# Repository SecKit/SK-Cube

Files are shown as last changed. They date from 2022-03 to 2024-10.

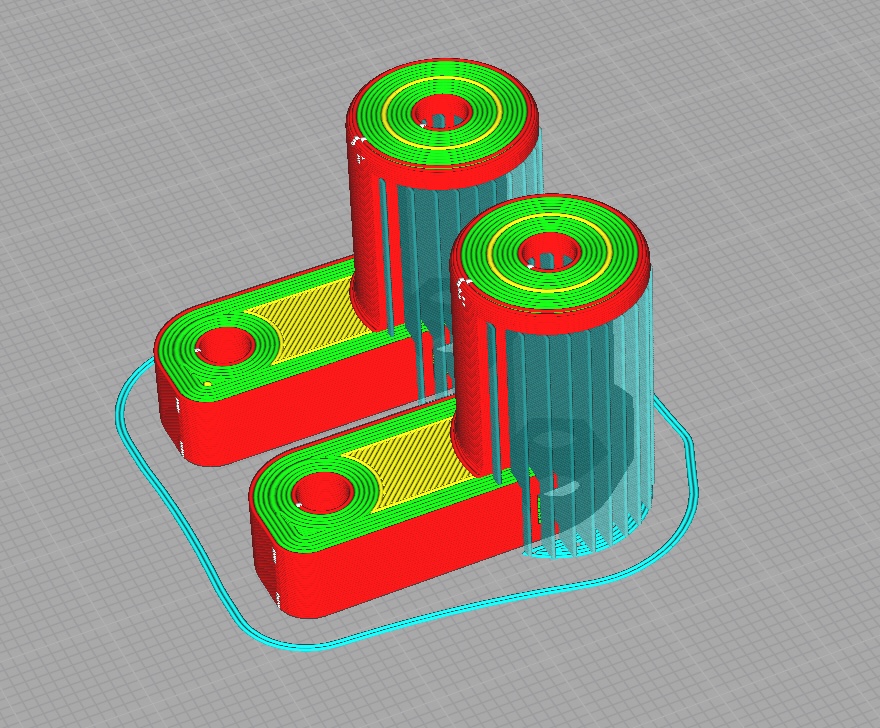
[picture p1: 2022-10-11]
STEP files/optional/secondary XY belt tensioner/z_slicing orientation.jpg

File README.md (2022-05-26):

## SK-Cube CoreXY 3D Printer

### Website
https://seckit3dp.design/price/sk-cube

### Wiki: Assembly Manual, tuning guide, etc.
https://sites.google.com/view/seckit-wiki/sk-cube-200x200x200/assembly-manual/sk-cube-assembly-manual

### Join SecKit's FaceBook group for owner's discussion and latest update
https://www.facebook.com/groups/SecKitCoreXY3DP/

### YouTube
https://www.youtube.com/channel/UCJUHiJfgDE5aeqbk4iZBPHA/videos

### FaceBook Page
https://www.facebook.com/seckit.3dp

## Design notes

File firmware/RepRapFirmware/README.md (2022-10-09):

1. Use a max 32G FAT32-format micro SD card. A 64GB or larger card is not supported.
2. Extract the zip file and copy all contents in "SK-Cube RRF" directory to the root of a micro SD card.
3. Follow the quick steps in the [Firmware Chapter](https://sites.google.com/view/seckit-wiki/sk-tank-350x350x400/assembly-manual/sk-tank-assembly-manual/12-firmware) of [SK-Tank Assembly Manual](https://sites.google.com/view/seckit-wiki/sk-tank-350x350x400/assembly-manual/sk-tank-assembly-manual) to flash the firmware to your control board.

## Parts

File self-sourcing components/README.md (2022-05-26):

Self-sourcing components for SK-Cube Barebones Kit.

|Category  |Item | #|Electrical req. |Mechanical req. |
|---|:---|-:|:---|:---|
|Power |Meanwell LRS-200-24 PSU | 1|200 or 350 watt, 24V output |4 holes on the bottom panel (PS.)|
|Power |SSR DC-AC | 1|At least 10 amp AC |2 holes on the bottom panel |
|Power |FS-101 fuse box and fuse | 1|6A for 110V. 3A for 220V. |1 hole on the bottom panel |
|Power |Power switch | 1| | |
|Power |Power cord | 1|At least 0.75 mm^2 internal wire |150cm or longer |
|Control |BigTreeTech Octopus or GTR | 1|At least 6 driver slots |4 holes on back panel |
|Control |TMC2225 | 6|(or other drivers) | |
|Stepper |NEMA17 1.8°/0.9° stepper for XY | 2|Common NEMA 17 stepper | |
|Stepper |NEMA17 1.8° pancake stepper for E | 1|Common NEMA 17 pancake stepper |(PPS.) |
|Extruder  |BMG or Hemera extruder | 1|(PPS.) | |
|Fan |4010 fan for driver cooling | 1|24V | |
|Fan |4020 blower for part cooling | 1|24V | |
|Sensor |Filament runout sensor | 1|(optional) | |
|Accessory |PTFE tube 3mm ID, 40cm | 1| | |
|Accessory |Cable tie |20| | |
|Accessory |Cable management nylon sleeve, wrapper, etc.| 1| | |

PS. Pre-drilled holes are there on the ACM (Aluminum Composite Material) back panel but you can still drill customized holes easily.

PPS. Use your preferred extruder and design a customized adapter based on [SK-Tank BMG adapter STEP file](https://github.com/SecKit/SK-Tank/tree/master/STEP%20files/extruder%20adapter%20-%20BMG) and [SK-Tank extruder carriage STEP file](https://github.com/SecKit/SK-Tank/tree/master/STEP%20files/extruder%20carriage). SK-Cube and SK-Tank share the same part cooling fan duct.

*SecKit will not be responsible for your self-sourcing items.*

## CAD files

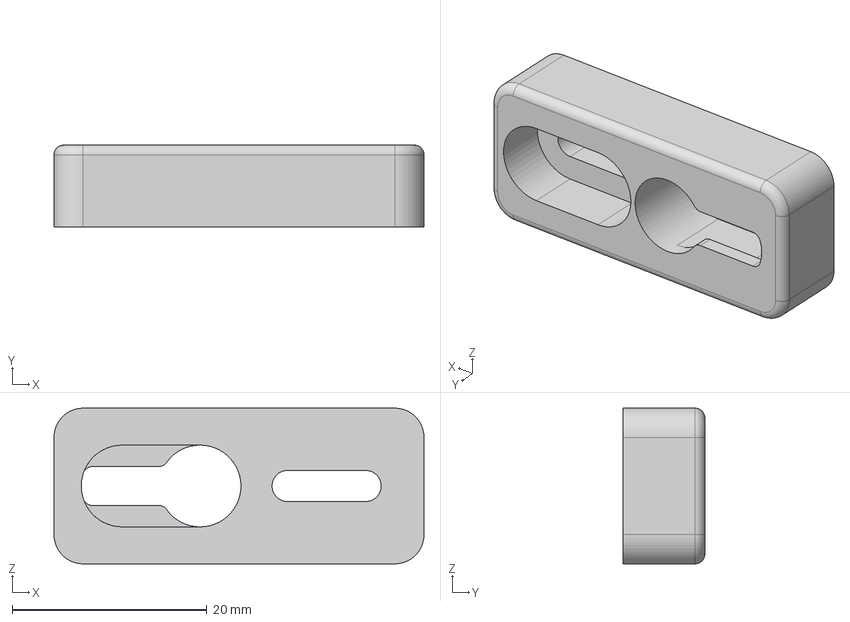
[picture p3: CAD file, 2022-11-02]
STEP files/must/bed expansion mount/bed expansion mount.step
38.0 x 8.40 x 16.0 mm

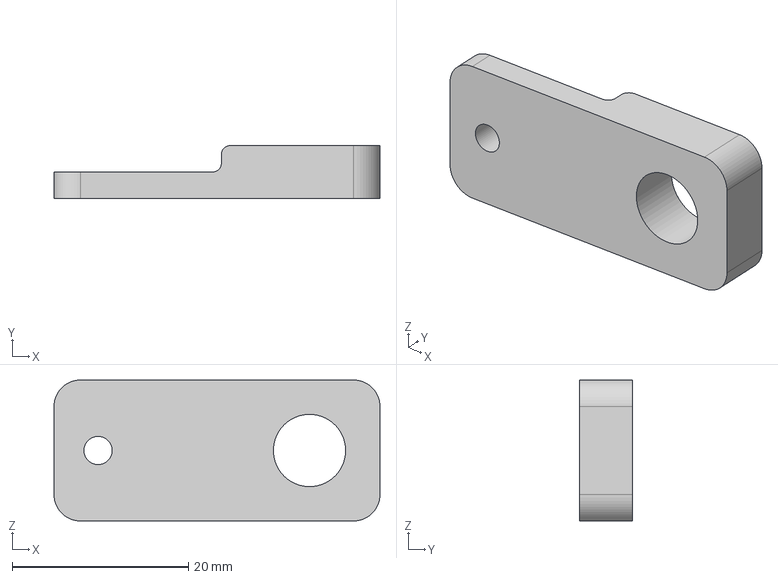
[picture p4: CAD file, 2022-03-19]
STEP files/must/bed fixed mount/bed fixed mount.step
37.0 x 6.00 x 16.0 mm

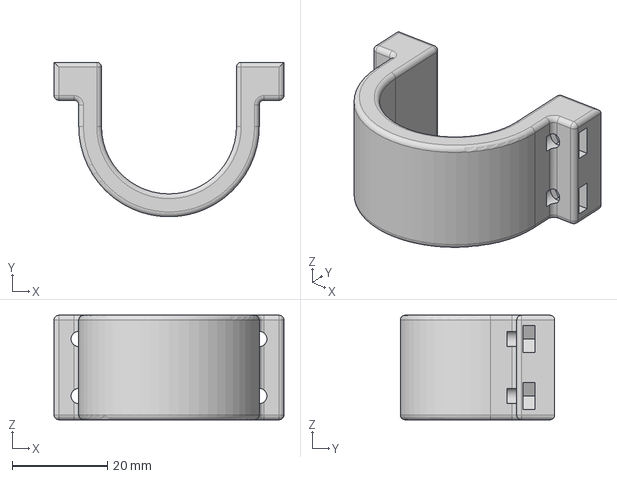
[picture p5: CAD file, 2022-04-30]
STEP files/must/Belted-Z stepper holder/NEMA8 gearbox bracket.step
48.4 x 32.5 x 22.0 mm

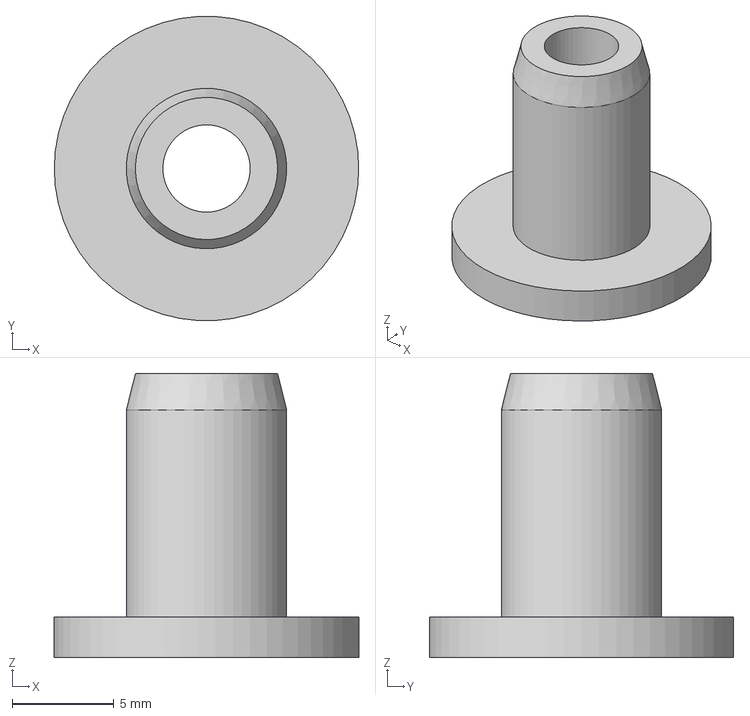
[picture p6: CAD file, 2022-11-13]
STEP files/must/filament PTFE guide holder/filament PTFE guide holder.step
15.0 x 15.0 x 14.0 mm

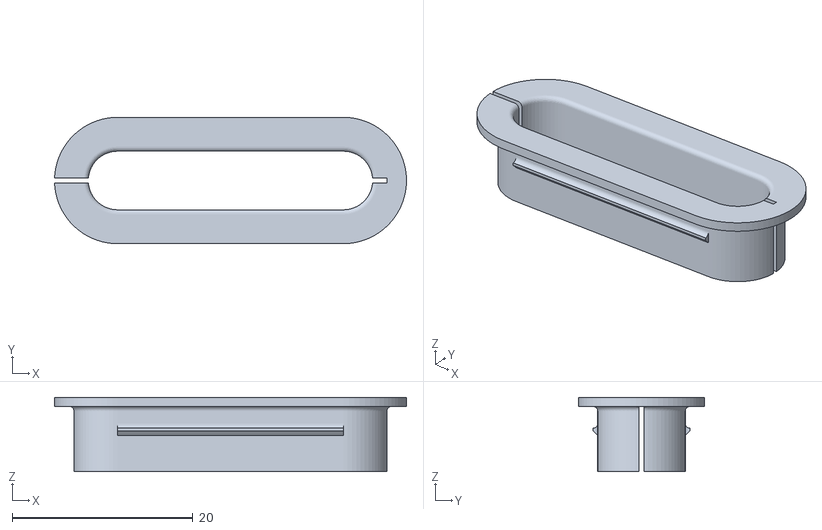
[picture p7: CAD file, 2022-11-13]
STEP files/must/grommets for wires/rear top.stl
39.0 x 14.0 x 8.20

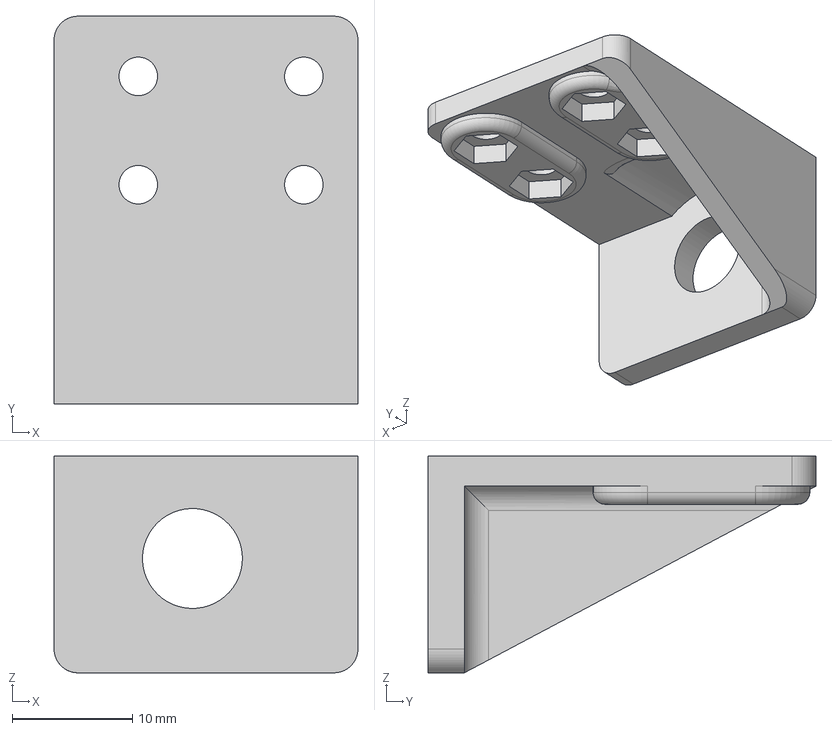
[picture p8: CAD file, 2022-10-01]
STEP files/must/inductive sensor mount/inductive sensor mount - Volcano hotend.step
25.3 x 32.2 x 18.0 mm

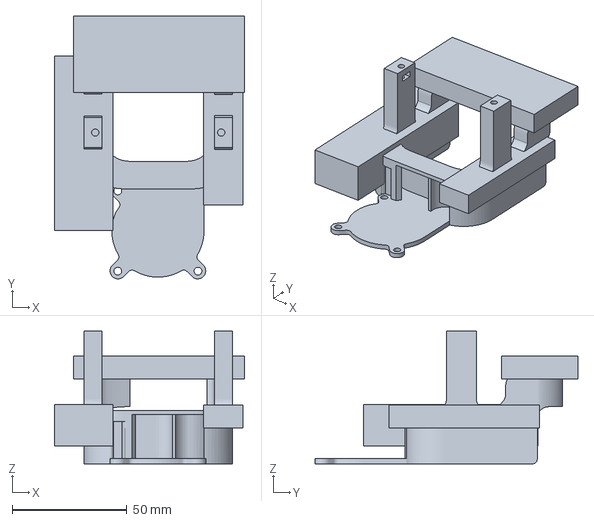
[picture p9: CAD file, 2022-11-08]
STEP files/must/part cooling fan duct/Volcano hotend/Cura 5.1.1 project of a SK-Cube fan duct + Volcano hotend.3mf
83.0 x 114.8 x 57.9 mm

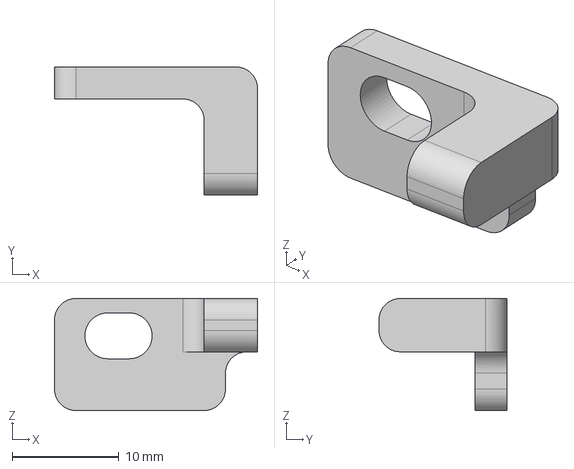
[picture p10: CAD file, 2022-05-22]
STEP files/must/X endstop finger/X endstop finger.step
19.0 x 12.0 x 10.5 mm

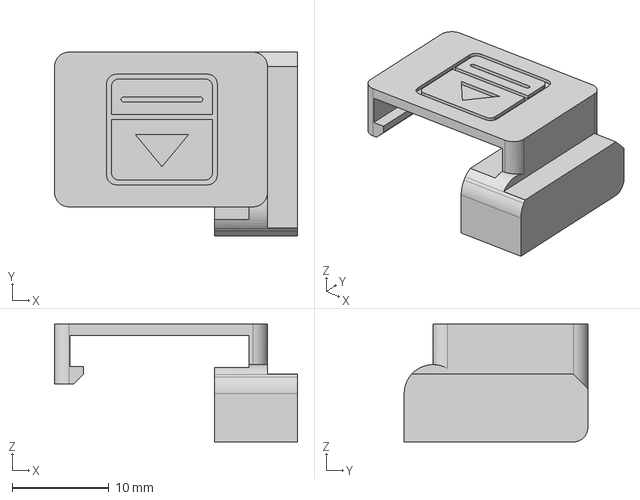
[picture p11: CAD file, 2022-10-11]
STEP files/must/X endstop trigger cap/X endstop trigger cap - for Breezer remote cooling duct.step
25.1 x 19.0 x 12.2 mm

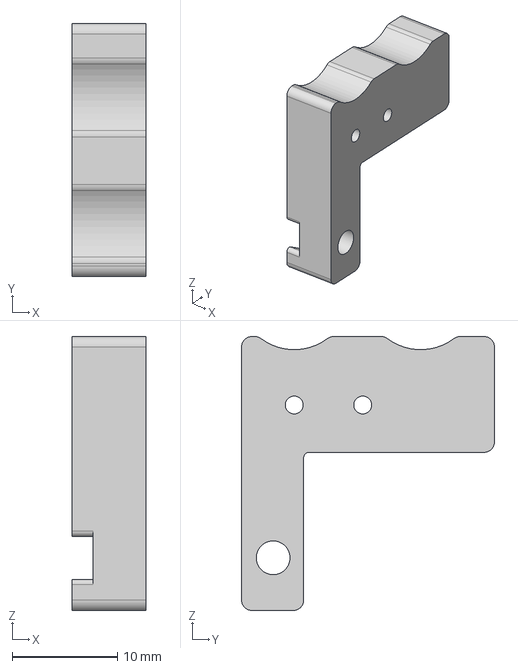
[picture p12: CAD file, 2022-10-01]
STEP files/must/Y-min endstop mount/Y-min endstop mount - right.step
7.00 x 24.0 x 26.0 mm

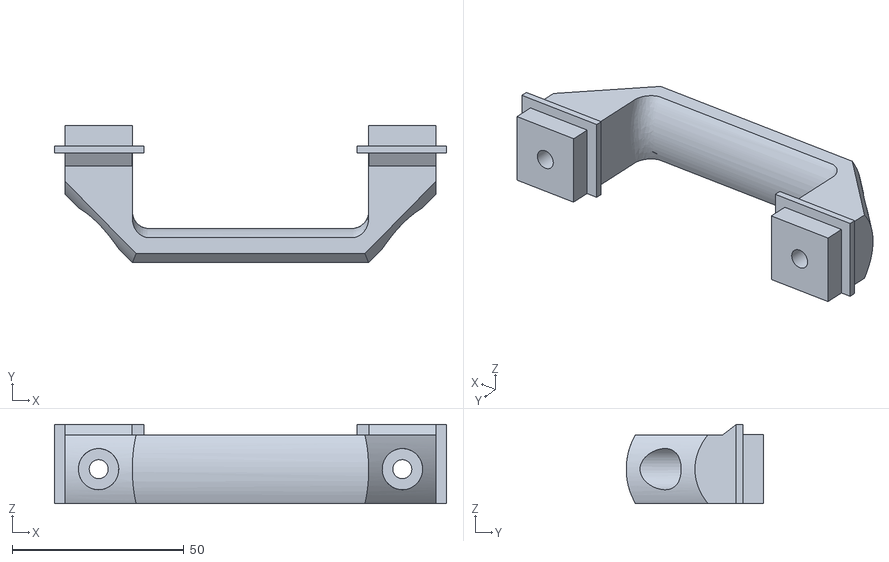
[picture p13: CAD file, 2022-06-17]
STEP files/optional/carry handle/handle_by Jeffery Kilgore.stl
114.0 x 40.0 x 23.0

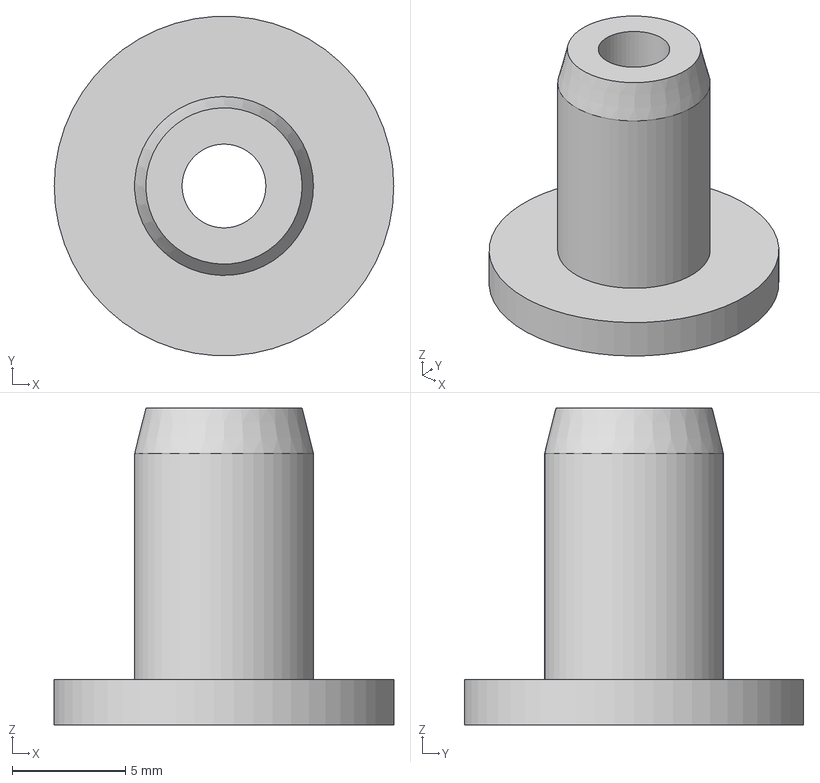
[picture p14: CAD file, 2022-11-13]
STEP files/optional/chamber thermistor holder/chamber temp sensor holder.step
15.0 x 15.0 x 14.0 mm

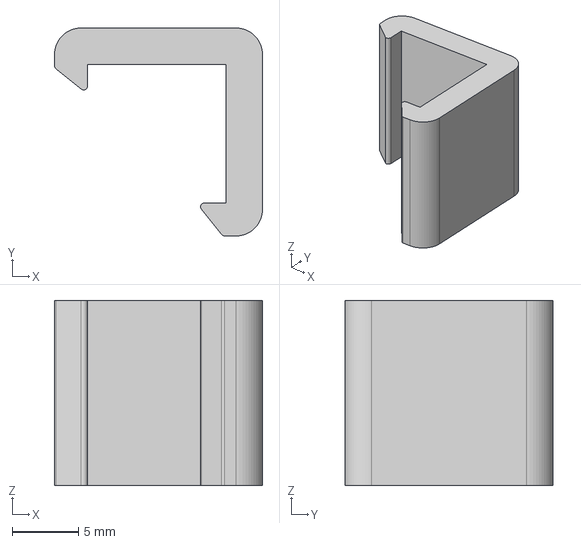
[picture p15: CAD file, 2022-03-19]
STEP files/optional/panel clamp/panel clamp.step
15.7 x 15.7 x 14.0 mm

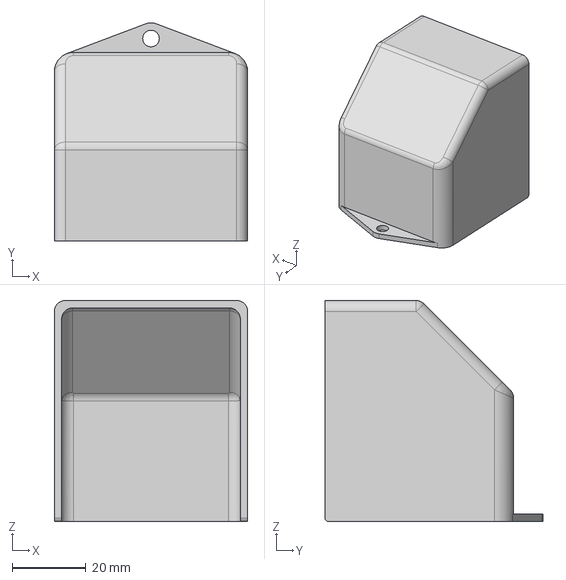
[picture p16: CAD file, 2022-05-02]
STEP files/optional/power switch cap/Power switch cap.step
52.5 x 59.2 x 60.0 mm

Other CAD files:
STEP files/optional/filament PTFE guide holder/filament PTFE guide holder.step
STEP files/optional/PTC heater box - easy print/panel_rear.stl
STEP files/optional/PTC heater box/Activated charcoal cartridge/3_0mm cover A.step
STEP files/optional/PTC heater box/PTC heater box.step
STEP files/must/Belted-Z stepper holder/NEMA8 gearbox bracket.stl
STEP files/must/Belted-Z stepper holder/square nut/NEMA8 gearbox bracket - square nut.step
STEP files/must/Belted-Z stepper holder/square nut/NEMA8 gearbox bracket - square nut.stl
STEP files/must/X endstop finger/X endstop finger.stl
STEP files/must/X endstop trigger cap/X endstop trigger cap - for Breezer remote cooling duct.stl
STEP files/must/X endstop trigger cap/X endstop trigger cap.step
STEP files/must/X endstop trigger cap/X endstop trigger cap.stl
STEP files/must/X endstop trigger cap/deprecated/X endstop finger.stl
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

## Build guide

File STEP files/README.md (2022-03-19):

Slicing tips

Printed files are all non-structural components so a common PLA or PETG filament with 0.4mm nozzle and 0.2mm layer height will do. Use ABS/ASA if your printer is enclosed. For special slicing settings please refer to the README.md file and print orientation pictures in each STL directory.   

All designs in this directory and subdirectories are shared under [CC BY-NC-SA 4.0](https://creativecommons.org/licenses/by-nc-sa/4.0/)

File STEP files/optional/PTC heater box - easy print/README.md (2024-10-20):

Slicer settings

|Setting |Description |
|:---|:---|
|Quantity |1 |
|Wall thickness |2mm |
|Infill |20% |
|Support |No |

ABS/ASA, 0.4mm nozzle, 0.2mm layer height

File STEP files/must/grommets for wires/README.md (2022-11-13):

Slicer settings

The gap in each grommet allows wire to pass after printer assembled.

|Setting |Description |
|:---|:---|
|Quantity |2, except the rear top one |
|Wall thickness |2mm |
|Infill |100% |
|Support |None |

PLA/PETG, 0.4mm nozzle, 0.2mm layer height

Use ABS/ASA if printer is enclosed.

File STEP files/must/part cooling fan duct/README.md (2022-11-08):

Slicer settings

|Setting |Description |
|:---|:---|
|Quantity |1 |
|Wall thickness |1.6 mm |
|Infill |40% |
|Support |20% with support blockers |

PLA/PETG, 0.4mm nozzle, 0.2mm layer height

Use ABS/ASA if printer is enclosed.

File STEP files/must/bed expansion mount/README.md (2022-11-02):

Slicer settings

|Setting |Description |
|:---|:---|
|Quantity |1 |
|Wall thickness |2mm |
|Infill |100% |
|Support |Yes |

PLA/PETG, 0.4mm nozzle, 0.2mm layer height

Use ABS/ASA if printer is enclosed.

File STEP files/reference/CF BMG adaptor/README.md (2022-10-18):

BMG adaptor is the plate between NEMA17 pancake stepper and BMG extruder, providing a mounting base to the CoreXY motion.

In case that some extruders have heat sink integrated so the overall length are shorter, you might have to lower the mounting holes for the stepper so the nozzle can still touch the build surface at Z=0.

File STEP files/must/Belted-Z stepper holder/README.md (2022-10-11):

Slicer settings

For kit sent after Oct 15, 2022, please use the square nut version. M3 square nuts are included in the kits.

|Setting |Description |
|:---|:---|
|Quantity |3 |
|Wall thickness |2.8mm |
|Infill |100% |
|Support |None |

PLA/PETG, 0.4mm nozzle, 0.2mm layer height

Use ABS/ASA if printer is enclosed.

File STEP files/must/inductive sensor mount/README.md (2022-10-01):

Slicer settings

Please choose the Volcano or the V6 version based on your hotend.

|Setting |Description |
|:---|:---|
|Quantity |1 |
|Wall thickness |2mm |
|Infill |100% |
|Support |None |

PLA/PETG, 0.4mm nozzle, 0.2mm layer height

Use ABS/ASA if printer is enclosed.

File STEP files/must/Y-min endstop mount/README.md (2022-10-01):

Slicer settings

Only the right one is necessary. The left one is optionally acting as a physical Y-min stopper.

|Setting |Description |
|:---|:---|
|Quantity |1 |
|Wall thickness |2mm |
|Infill |100% |
|Support |None |

PLA/PETG, 0.4mm nozzle, 0.2mm layer height

Use ABS/ASA if printer is enclosed.

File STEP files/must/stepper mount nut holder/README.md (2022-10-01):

Slicer settings

|Setting |Description |
|:---|:---|
|Quantity |2 |
|Wall thickness |2mm |
|Infill |20% |
|Support |None |

PLA/PETG, 0.4mm nozzle, 0.2mm layer height

Use ABS/ASA if printer is enclosed.

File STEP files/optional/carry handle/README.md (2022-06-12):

Slicer settings

|Setting |Description |
|:---|:---|
|Quantity |2 |
|Wall thickness |2mm |
|Infill |100% |
|Support |Optional |

PLA/PETG, 0.4mm nozzle, 0.2mm layer height

Use ABS/ASA if printer is enclosed.

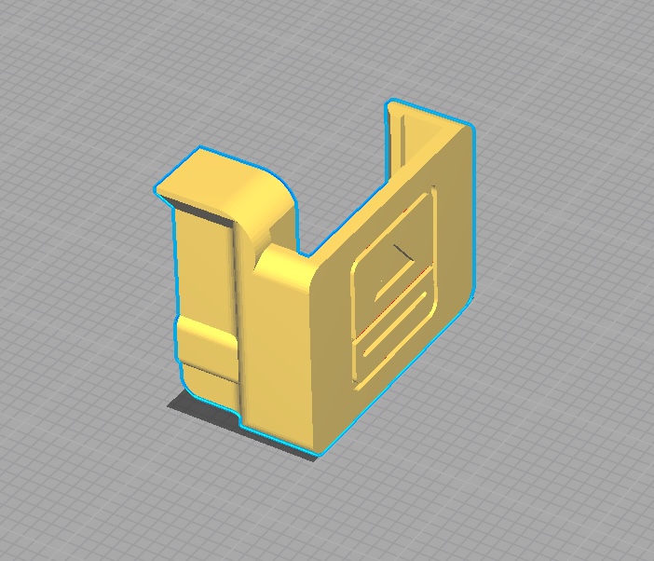
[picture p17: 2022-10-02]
STEP files/must/X endstop trigger cap/z_slicing orientation.jpg

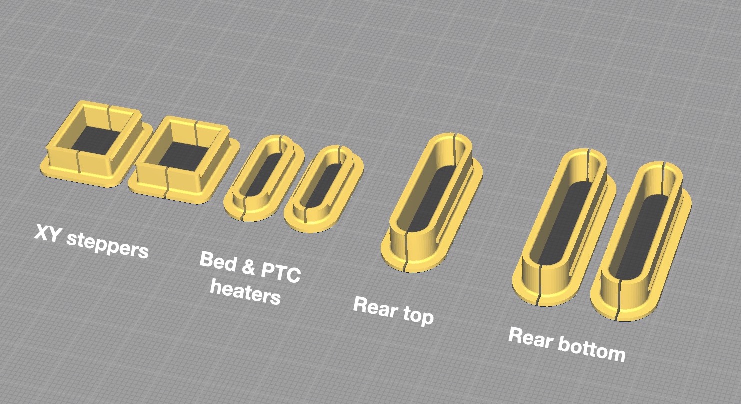
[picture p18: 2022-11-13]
STEP files/must/grommets for wires/z_slicing orientation.jpg

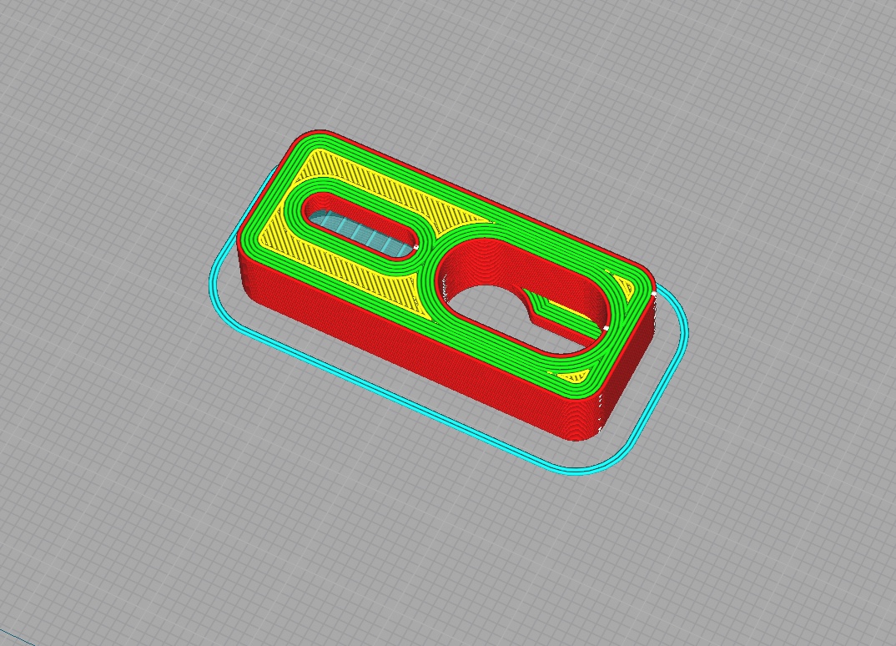
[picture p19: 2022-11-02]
STEP files/must/bed expansion mount/z_print orientation 1.jpg

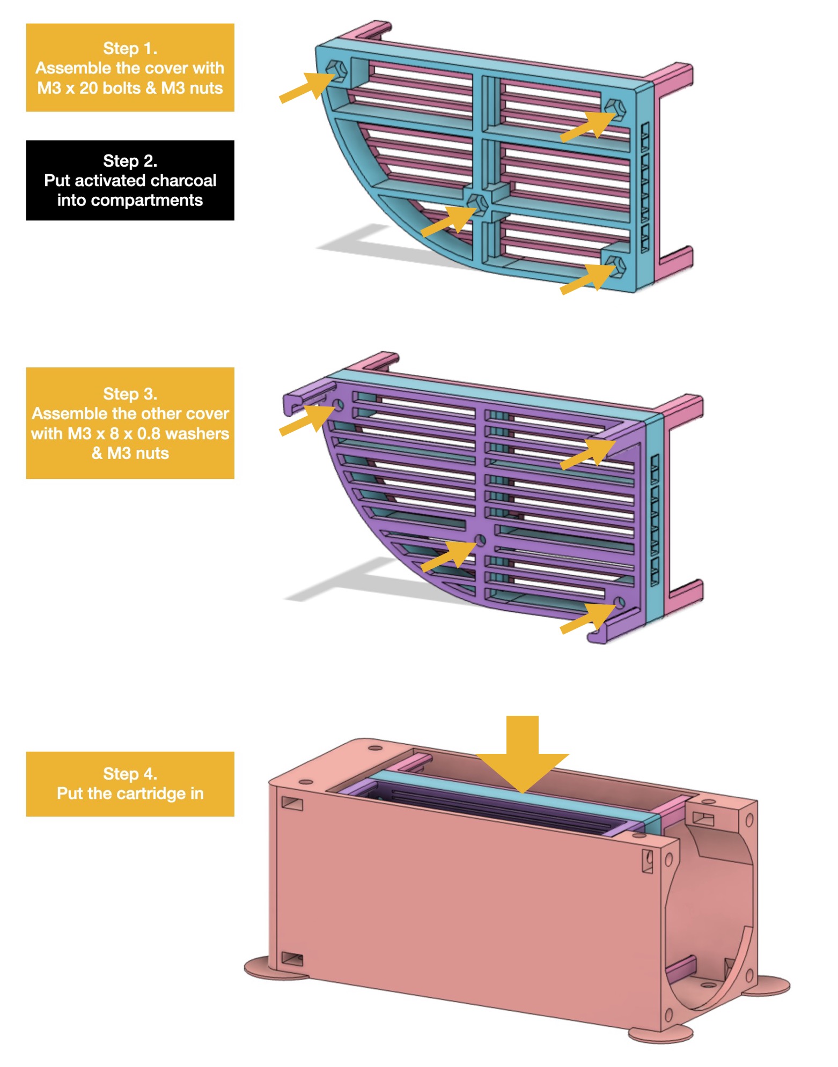
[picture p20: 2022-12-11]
STEP files/optional/PTC heater box/Activated charcoal cartridge/usage_2.jpg

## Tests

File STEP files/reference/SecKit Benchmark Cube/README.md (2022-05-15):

## SecKit Benchmark Cube
A 30x30 benchmarking cube to check dimensional accuracy, overhangs, retraction/stringing, ringing, and more.

#### Outer dimension
30x30x30 mm^3

#### Wall thickness
3 mm

#### Overhang angles
- Triangle: 30°
- Hexagon: 30°
- Nonagon: 10°,  50°

#### Gap widths
0.4 mm, 0.3 mm, 0.2 mm, 0.15 mm, 0.1 mm

#### Author
Alan Kilgore, Ernest Lin

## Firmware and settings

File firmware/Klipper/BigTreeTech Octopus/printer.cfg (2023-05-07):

[include fluidd.cfg]

########################################
# Basic settings
########################################
[mcu]
serial: /dev/serial/by-id/usb-Klipper_stm32f429xx_440027001050533850353920-if00
#restart_method: command
# setup for PA9, PA10 USART1_tx / rx directly connected to the RPI GPIO TX / RX pins
# These are the pins the OctoPus uses for its built in RPI 40 pin connector
# only connect GND, TX, RX - supply 5v power to the RPI separately
# do not cross over TX/RX - it is done internally on the OctoPus PCB.
# Use "sudo raspi-config" to disable the serial terminal - but enable the serial port.
# When running "make menuconfig" you must un-select the USB Serial check box

[printer]
kinematics: corexy
max_velocity: 300
max_accel: 5000 ;set to 7000 for resonance test
max_z_velocity: 7
max_z_accel: 100
square_corner_velocity: 5.0

# Note: Extruder settings have to be set in on the extruder in the Steppers and Stepper 
# Drivers section usig "max_extrude_only_velocity:" and "max_extrude_only_accel:" attributes

########################################
# Steppers and Stepper Drivers
########################################
# using TMC2208 configuration for TMC2225 steper drivers

# Lower belt stepper left back
# using driver 0 on Octopus Pro
[stepper_x]
step_pin: PF13
dir_pin: !PF12	# ! to reverse for standard Tank wiring?
enable_pin: !PF14
microsteps: 16
rotation_distance: 32 # Marlin/RRF reference: 200 steps / mm (rotation_distance = <full_steps_per_rotation> * <microsteps> / <steps_per_mm>)
full_steps_per_rotation: 200 # 400 for a 0.9 stepper, 200 for 1.8 stepper
endstop_pin: PG6
position_endstop: -1
position_min: -1
position_max: 210
homing_speed: 80

# Upper belt stepper right back
# using driver 1 on Octopus Pro
[stepper_y]
step_pin: PG0
dir_pin: !PG1	# ! to reverse for standard Tank wiring?
enable_pin: !PF15
microsteps: 16
rotation_distance: 32 # Marlin/RRF reference: 200 steps / mm (rotation_distance = <full_steps_per_rotation> * <microsteps> / <steps_per_mm>)
full_steps_per_rotation: 200 # 400 for a 0.9 stepper, 200 for 1.8 stepper
endstop_pin: PG9
position_endstop: -1
position_min: -1
position_max: 205
homing_speed: 80

# Z stepper front left
# using driver 2 on Octopus Pro
[stepper_z]
step_pin: PF11
dir_pin: PG3
enable_pin: !PG5
microsteps: 16
rotation_distance: 40 # 40 for 20T driving pulley, 32 for 16T
full_steps_per_rotation: 200 # for a 1.8 stepper
gear_ratio: 20:1 # to match z stepper 20:1 gearbox NEMA8
endstop_pin: probe:z_virtual_endstop # use BL-Touch or inductive probe for Z endstop
position_min: -5
position_max: 200
homing_retract_dist: 2 # added to lift the nozzle 2mm after homing vs. endstop

# Z1 stepper front right
# using driver 3 on Octopus Pro
[stepper_z1]
step_pin: PG4
dir_pin: !PC1 # direction inverted since SK-Tank setup is using flipped stepper orientation for Z1 
enable_pin: !PA0
microsteps: 16
rotation_distance: 40 # 40 for 20T driving pulley, 32 for 16T
full_steps_per_rotation: 200 # for a 1.8 stepper
gear_ratio: 20:1 # to match z stepper 20:1 gearbox NEMA8

# Z2 stepper back center
# using driver 4 on Octopus Pro
[stepper_z2]
step_pin: PF9
dir_pin: PF10
enable_pin: !PG2
microsteps: 16
rotation_distance: 40 # 40 for 20T driving pulley, 32 for 16T
full_steps_per_rotation: 200 # for a 1.8 stepper
gear_ratio: 20:1 # to match z stepper 20:1 gearbox NEMA8

# Extruder
# using driver 5 on Octopus Pro
[extruder]
step_pin: PC13
dir_pin: !PF0
enable_pin: !PF1
microsteps: 16 # values set for Biqu H2
rotation_distance: 7.71 # Triangle Lab BMG clone
full_steps_per_rotation: 200 # for a 1.8 stepper
nozzle_diameter: 0.400
filament_diameter: 1.750
max_extrude_only_distance: 100.0
min_extrude_temp: 170
min_temp: 0
max_temp: 260
pressure_advance: 0.054
heater_pin: PA2		# HE0, heater 0
sensor_pin: PF4		# J45, sensor 1 (T0)


# Thermistor - Triangle Lab BMG
sensor_type: ATC Semitec 104NT-4-R025H42G
control: pid # changed to "watermark" and comment/delete the PID settings below if you have issues with the SSR (like some SSR dont like PID control)
# Adjusted by running PID_CALIBRATE HEATER=extruder TARGET=205
pid_Kp: 24.921
pid_Ki: 1.093
pid_Kd: 142.050

########################################
# Heaters and Fans
########################################

[heater_bed]
heater_pin: PA1
sensor_pin: PF3		# J44, sensor 0 (TB)
sensor_type: Generic 3950
control: pid
# Adjusted by running PID_CALIBRATE HEATER=heater_bed TARGET=60
pid_Kp: 53.190
pid_Ki: 2.955
pid_Kd: 239.354
min_temp: 0
max_temp: 110

[fan]
pin: PA8 # FAN0

[heater_fan Hotend]
pin: PE5 	# FAN1
heater: extruder
heater_temp: 50.0

#[heater_generic Chamber_heater]
#gcode_id: 8
##   The id to use when reporting the temperature in the M105 command.
##   This parameter must be provided.
#heater_pin: PA3    # HE1
#sensor_type: ATC Semitec 104NT-4-R025H42G
#sensor_pin: PF5		# T1
#control: pid
#pid_Kp: 24.921
#pid_Ki: 1.093
#pid_Kd: 142.050
## max_power ranges between 0.0 ~ 1.0. 
## Lower this if the thermal switch piggy-backed on 
## the PTC heater activates frequently.
#max_power: 0.5		
#min_temp: 0
#max_temp: 170

[fan_generic Chamber_heater_fan]
pin: PD12

[fan_generic HEPA_filter_fan]
pin: PD13

[temperature_sensor mcu_temp]
sensor_type: temperature_mcu

########################################
# Inductive sensor
########################################

[probe]
pin: PG10
x_offset: 0.0    # BMG/Dragon stock
y_offset: 35.0     # BMG/Dragon stock
z_offset: 0.75
speed: 7.5  #   Speed (in mm/s) of the Z axis when probing. The default is 5mm/s.
samples: 1

########################################
# BL-Touch
########################################

# [bltouch]
# sensor_pin: ^PB7
# control_pin: PB6
# pin_move_time: 0.4
# stow_on_each_sample: True
# probe_with_touch_mode: True #Needed for BLTouch V3.0 / V3.1
# x_offset: -29.2
# y_offset: 36
# z_offset: 3.75
# speed: 5
# samples: 1
# sample_retract_dist: 2
# samples_result: average

[safe_z_home]
home_xy_position: 10,10 # Nozzle coordinates that will put the probe in the center of the bed
speed: 150
z_hop: 10                 # Move up 10mm
z_hop_speed: 7.5

[bed_mesh]
speed: 150
horizontal_move_z: 6
mesh_min: 20,35     #Probe coordinates
mesh_max: 180,195   #Probe coordinates
probe_count: 5,5
algorithm: bicubic
bicubic_tension: 0.2
move_check_distance: 5
split_delta_z: .025
fade_start: 1
fade_end: 10
#fade_target: 0

[z_tilt]
#Positions of the bed mounts, in nozzle coordinates. Shouldn't need to change these once set up.
z_positions:
	3, 3
	215, 3
    110, 217
#Positions to measure, in nozzle coordinates - i.e. make sure the probe is above the bed when the nozzle is at these positions
points:
	10, 0
	195, 0
    100, 160
speed: 150
horizontal_move_z: 10
retries: 2
retry_tolerance: 0.1

#[force_move]
#enable_force_move: True #   Set to true to enable FORCE_MOVE and SET_KINEMATIC_POSITION

#[firmware_retraction]

########################################
# Input Shaping
########################################
#[mcu rpi]
#serial: /tmp/klipper_host_mcu

#[adxl345]
#cs_pin: rpi:None

#[resonance_tester]
#accel_chip: adxl345
#probe_points:
#    100,100,20  # an example

#[input_shaper]
# Biqu H2
#shaper_freq_x: 74.0
#shaper_type_x: mzv
#shaper_freq_y: 82.4
#shaper_type_y: 2hump_ei

# BMG/Dragon HF - Aluminum gantry
#shaper_freq_x: 61.6
#shaper_type_x: mzv
#shaper_freq_y: 46.4
#shaper_type_y: mzv

# BMG/Dragon HF - CF gantry - stock
#shaper_freq_x: 60.0
#shaper_type_x: zv
#shaper_freq_y: 52.0
#shaper_type_y: zv

# BMG/Dragon HF - CF gantry - dual 5015s
#shaper_freq_x: 66.2
#shaper_type_x: mzv
#shaper_freq_y: 48.6
#shaper_type_y: mzv


########################################
# TMC2208 configuration
########################################

#[tmc2208 stepper_x]	# Disabled for MKS Servo42C
#uart_pin: PC4
#interpolate: True
#run_current: 0.800
#hold_current: 0.500

#[tmc2208 stepper_y]	# Disabled for MKS Servo42C
#uart_pin: PD11
#interpolate: True
#run_current: 0.800
#hold_current: 0.500

[tmc2208 stepper_z]
uart_pin: PC6
interpolate: True
run_current: 0.500
hold_current: 0.400

[tmc2208 stepper_z1]
uart_pin: PC7
interpolate: True
run_current: 0.500
hold_current: 0.400

[tmc2208 stepper_z2]
uart_pin: PF2
interpolate: True
run_current: 0.500
hold_current: 0.400

[tmc2208 extruder]
uart_pin: PE4
interpolate: True
run_current: 0.800
hold_current: 0.300


########################################
# EXP1 / EXP2 (display) pins
########################################

#[board_pins]
#aliases:
#    # EXP1 header
#    EXP1_1=PE8, EXP1_2=PE7,
#    EXP1_3=PE9, EXP1_4=PE10,
#    EXP1_5=PE12, EXP1_6=PE13,    # Slot in the socket on this side
#    EXP1_7=PE14, EXP1_8=PE15,
#    EXP1_9=<GND>, EXP1_10=<5V>,
#
#    # EXP2 header
#    EXP2_1=PA6, EXP2_2=PA5,
#    EXP2_3=PB1, EXP2_4=PA4,
#    EXP2_5=PB2, EXP2_6=PA7,      # Slot in the socket on this side
#    EXP2_7=PC15, EXP2_8=<RST>,
#    EXP2_9=<GND>, EXP2_10=<5V>

# See the sample-lcd.cfg file for definitions of common LCD displays.
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

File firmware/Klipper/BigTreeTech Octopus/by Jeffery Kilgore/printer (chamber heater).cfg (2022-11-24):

[mcu]
serial: /dev/serial/by-id/usb-Klipper_(your mcu serial should go here)

[display_status]

[virtual_sdcard]
path: ~/gcode_files

[printer]
kinematics: corexy
max_velocity: 350  
max_accel: 8000    			
max_accel_to_decel: 4000		#Klipper recommends 1/2 of max_accel
max_z_velocity: 8 			#Max 15 for 12V TMC Drivers, can increase for 24V
max_z_accel: 200
square_corner_velocity: 6.0

[mcu rpi]
serial: /tmp/klipper_host_mcu

[adxl345]
cs_pin: rpi:None

[resonance_tester]
accel_chip: adxl345
probe_points:
    100,100,20  # an example

[temperature_sensor raspberry_pi]
sensor_type: temperature_host
min_temp: 10
max_temp: 100

[probe]
##	Inductive Probe
##	This probe is not used for Z height, only Quad Gantry Leveling
pin: ~PB7
x_offset: 0
y_offset: 25.0
#z_offset: 0.200
speed: 3.5
samples: 3
samples_result: median
sample_retract_dist: 4.0
samples_tolerance: 0.01
samples_tolerance_retries: 3

[safe_z_home]
home_xy_position: 100,100 # Change coordinates to the center of your print bed
speed: 100
z_hop: 10                 # Move up 10mm
z_hop_speed: 7.5

#####################################################################
# 	X/Y Stepper Settings
#####################################################################

[stepper_x]
step_pin: PG0
dir_pin: !PG1
enable_pin: !PF15
rotation_distance: 32 # was 32 default @ 16 microsteps
microsteps: 16 #16 Default
full_steps_per_rotation: 200  #set to 400 for 0.9 degree stepper - default
endstop_pin: PG6
position_min: -5
position_endstop: -5
position_max: 205 
homing_speed: 50  #Max 100
homing_retract_dist: 5
#step_pulse_duration: 0.000002000
#   The minimum time between the step pulse signal edge and the
#   following "unstep" signal edge. This is also used to set the
#   minimum time between a step pulse and a direction change signal.
#   The default is 0.000000100 (100ns) for TMC steppers that are
#   configured in UART or SPI mode, and the default is 0.000002 (which
#   is 2us) for all other steppers.



## X Stepper on MOTOR0(B Motor)
[stepper_y]
step_pin: PF13
dir_pin: !PF12
enable_pin: !PF14
rotation_distance: 32 #was 32 default
microsteps: 16 # 16 default
full_steps_per_rotation: 200  #set to 400 for 0.9 degree stepper -default
endstop_pin: PG9 #pg9
position_min: -0
position_endstop: -0
position_max: 200 
homing_speed: 50   #Max 100
homing_retract_dist: 5
#step_pulse_duration: 0.000002000
#   The minimum time between the step pulse signal edge and the
#   following "unstep" signal edge. This is also used to set the
#   minimum time between a step pulse and a direction change signal.
#   The default is 0.000000100 (100ns) for TMC steppers that are
#   configured in UART or SPI mode, and the default is 0.000002 (which
#   is 2us) for all other steppers.
 
#####################################################################
# 	Z Stepper Settings
#####################################################################

## Z0 Stepper - Front Left on MOTOR2_1
[stepper_z]
step_pin: PF11
dir_pin: PG3
enable_pin: !PG5
rotation_distance: 32
gear_ratio: 20:1
microsteps: 16
endstop_pin: probe:z_virtual_endstop
position_max: 200
position_min: -2
homing_speed: 12
second_homing_speed: 2
homing_retract_dist: 5

##	Make sure to update below for your relevant driver (2208 or 2209)
[tmc2209 stepper_z]
uart_pin: PC6
interpolate: true
run_current: 0.65
hold_current: 0.5
sense_resistor: 0.110
stealthchop_threshold: 0

##	Z1 Stepper - Rear Left on MOTOR3
[stepper_z1]
step_pin: PG4
dir_pin: PC1
enable_pin: !PA0
rotation_distance: 32
gear_ratio: 20:1
microsteps: 16

##	Make sure to update below for your relevant driver (2208 or 2209)
[tmc2209 stepper_z1]
uart_pin: PC7
interpolate: true
run_current: 0.65
hold_current: 0.5
sense_resistor: 0.110
stealthchop_threshold: 0

##	Z2 Stepper - Rear Right on MOTOR4
[stepper_z2]
step_pin: PF9
dir_pin: !PF10
enable_pin: !PG2
rotation_distance: 32
gear_ratio: 20:1
microsteps: 16


##	Make sure to update below for your relevant driver (2208 or 2209)
[tmc2209 stepper_z2]
uart_pin: PF2
interpolate: true
run_current: 0.65
hold_current: 0.5
sense_resistor: 0.110
stealthchop_threshold: 0

#####################################################################
# 	Extruder
#####################################################################

#	E0 on MOTOR6
[extruder]
step_pin: PE2
dir_pin: !PE3
enable_pin: !PD4
##	Update value below when you perform extruder calibration
##	If you ask for 100mm of filament, but in reality it is 98mm:
##	rotation_distance = <previous_rotation_distance> * <actual_extrude_distance> / 100
rotation_distance: 5.555	#Bondtech LGX Lite
microsteps: 16
full_steps_per_rotation: 200	#200 for 1.8 degree, 400 for 0.9 degree
nozzle_diameter: 0.400
filament_diameter: 1.75
heater_pin: PA2
##	Validate the following thermistor type to make sure it is correct
sensor_type: ATC Semitec 104NT-4-R025H42G
sensor_pin: PF4
min_temp: 0
max_temp: 305
max_power: 1.0
min_extrude_temp: 160
#control = pid
#pid_kp = 26.213
#pid_ki = 1.304
#pid_kd = 131.721
##	Try to keep pressure_advance below 1.0
pressure_advance: 0.05  #Default is 0.040

##	E0 on MOTOR6
##	Make sure to update below for your relevant driver (2208 or 2209)
[tmc2208 extruder]
uart_pin: PE1
interpolate: true
run_current: 0.65
hold_current: 0.4
sense_resistor: 0.110
stealthchop_threshold: 0


#####################################################################
# 	Bed Heater
#####################################################################

[heater_bed]
##	SSR Pin - BED_OUT
heater_pin: PA1
sensor_type: NTC 100K MGB18-104F39050L32
sensor_pin: PF3
##	Adjust Max Power so your heater doesn't warp your bed
max_power: 0.90
min_temp: 0
max_temp: 120
#control: pid
#pid_kp: 58.437
#pid_ki: 2.347
#pid_kd: 363.769

#####################################################################
# 	Fan Control
#####################################################################

[fan]
##	Print Cooling Fan - CNC_FAN0
pin: PA8
kick_start_time: 1.0
off_below: 0.10

[heater_fan hotend_fan]
##	Hotend Fan - CNC_FAN1
pin: PE5
max_power: 1.0
kick_start_time: 1.0
heater: extruder
heater_temp: 50.0
##	If you are experiencing back flow, you can reduce fan_speed
fan_speed: 1.0

#[controller_fan MCU_controller_fan]
#pin: PD12
#max_power: 0.45
#shutdown_speed: 0
#kick_start_time: 0.5
#idle_timeout: 30
#idle_speed: 0.40
#stepper: stepper_z, stepper_y, stepper_x, stepper_z2, stepper_z1, extruder

[heater_fan Chamber]
pin: PD12
max_power: 0.90
shutdown_speed: 0
kick_start_time: 0.5
heater: Chamber

[heater_generic Chamber]
gcode_id: chamber
#   The id to use when reporting the temperature in the M105 command.
#   This parameter must be provided.
heater_pin: PB10
max_power: 0.75
sensor_type: Generic 3950
sensor_pin: PF5
smooth_time: 1.0
control: watermark
#pid_Kp: 54.027
#pid_Ki: 0.770
#pid_Kd: 948.182
pwm_cycle_time: 0.3
min_temp: 0
max_temp: 55
#   See the "extruder" section for the definition of the above
#   parameters.

[verify_heater Chamber]
max_error: 120
check_gain_time: 120
hysteresis: 5
heating_gain: 1

#####################################################################
# 	LED Control
#####################################################################

#[output_pin caselight]
# Chamber Lighting - HE1 Connector (Optional)
#pin: PA3
#pwm:true
#shutdown_value: 0
#value:1
#cycle_time: 0.01

#####################################################################
# 	Homing and Gantry Adjustment Routines
#####################################################################

[idle_timeout]
timeout: 1800

[bed_mesh]
speed: 75
horizontal_move_z: 5
mesh_min: 10, 31
mesh_max: 190, 175
probe_count: 5,5
fade_start: 1
fade_end: 10
fade_target: 0

[z_tilt]
z_positions:
	-10, 0
	115, 225
    225, 0
points:
	15,1
	115, 160
    195, 1 #reset to 345, 10 when cable chain is fixed
speed: 100
horizontal_move_z: 10
retries: 5
retry_tolerance: 0.02


[force_move]
enable_force_move: True #   Set to true to enable FORCE_MOVE and SET_KINEMATIC_POSITION

[input_shaper]

########################################
# EXP1 / EXP2 (display) pins
########################################

[board_pins]
aliases:
    # EXP1 header
    EXP1_1=PE8, EXP1_2=PE7,
    EXP1_3=PE9, EXP1_4=PE10,
    EXP1_5=PE12, EXP1_6=PE13,    # Slot in the socket on this side
    EXP1_7=PE14, EXP1_8=PE15,
    EXP1_9=<GND>, EXP1_10=<5V>,

    # EXP2 header
    EXP2_1=PA6, EXP2_2=PA5,
    EXP2_3=PB1, EXP2_4=PA4,
    EXP2_5=PB2, EXP2_6=PA7,      # Slot in the socket on this side
    EXP2_7=PC15, EXP2_8=<RST>,
    EXP2_9=<GND>, EXP2_10=<5V>

#####################################################################
# 	Displays
#####################################################################

## 	Uncomment the display that you have
#--------------------------------------------------------------------

;[gcode_arcs]
;resolution: 0.1
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

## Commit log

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2022-03-24 bug fix: close the gap between air separator and rear wall.
    [SK-Go fan duct v2 + Volcano hotend + inductive ABL.step, SK-Go fan duct v2 + Volcano hotend + inductive ABL.stl]
2022-04-30 add NEMA8 Z gearbox stepper mount.
    [NEMA8 gearbox bracket.step, NEMA8 gearbox bracket.stl]
2022-05-02 Upload printed Y frame for Beta kit owners.
    [left Y frame.stl, right Y frame.stl]
2022-05-02 add printed z top pulley housing for beta kits
    [rear z top pulley housing.stl]
2022-05-02 move to the new directory
    [left Y frame.stl, right Y frame.stl]
2022-05-02 add the STL of power switch cap
    [Power switch cap.step, Power switch cap.stl]
2022-05-02 upload RRF for SK-Cube
    [1_Run G32 bed.g, bed.g, config.g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]
2022-05-05 differentiate left and right endstop mount
    [Y-min endstop mount - left.step, Y-min endstop mount - left.stl, Y-min endstop mount - right.step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]
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2022-05-07 add PTC heater box
    [PTC heater box.step, PTC heater box.stl]
2022-05-09 bug fix: the hole for the Y endstop mount was missed.
    [left Y frame.stl, right Y frame.stl]
2022-05-15 add SecKit Benchmark Cube
    [SecKit benchmark cube v10.stl]
2022-05-16 Align driver slot mappings to the SK-Cube online manual.
    [config.g]
2022-05-22 update endstop finger to prevent interference with the extruder carriage
    [X endstop finger.step, X endstop finger.stl]
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2022-06-03 Use meta commands introduced in RRF 3. Thank Budhi's update.
    [bed.g]
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2022-06-11 add a new printed part: filament PTFE guide holder
    [filament PTFE guide holder.step, filament PTFE guide holder.stl]
2022-06-12 add the frame handler
    [handle no support.step, handle with support.step, handler no support.stl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]
2022-06-17 add Klipper config file contributed by Jeffery Kilgore
    [printer (chamber heater).cfg]
2022-06-17 add another carry handle by Jeffery Kilgore
    [handle_by Jeffery Kilgore.stl]
2022-06-19 add another holder for flatten thermistor
    [flatten thermistor holder by Jeffery Kilgore.stl]
2022-07-03 add XY belt tensioners
    [XY belt tensioner.stl, XY belt tensioners.step]
2022-07-03 update Y-min endstop mount
    [Y-min endstop mount - left.step, Y-min endstop mount - left.stl, Y-min endstop mount - right.step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]
2022-07-03 Slow down XY homing speed to prevent damaging or moving microswitch endstop mounts
    [homeall.g, homex.g, homey.g]
2022-09-16 add a SK-Cube Klipper config file
    [printer.cfg]
2022-09-16 comment out chamber heater settings as default
    [printer.cfg]
2022-09-25 correct the board name to GTR
2022-10-01 Shrink bolt hole size according to Cube owner Zhao Weijie's suggestion.
    [Y-min endstop mount - left.step, Y-min endstop mount - left.stl, Y-min endstop mount - right.step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]
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2022-10-02 update X endstop trigger to a clip-on cap for easier installation
    [X endstop finger.step, X endstop finger.stl, X endstop trigger cap.step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]
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2022-10-07 add a newer design with micky mouse ears for easier print
    [PTC heater box - with micky mouse ears.step, PTC heater box - with micky mouse ears.stl]
2022-10-07 add a draft, non-working version copied from GTR board. To be modified later.
    [1_Run G32 bed.g, bed.g, config.g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]
2022-10-08 Extend fan duct arms 1.5mm to prevent collision with the BMG extruder
    [Cura 5.1.1 project of a SK-Cube fan duct v2 + Volcano hotend + inductive ABL for SK-Cube.3mf, Cura project of a SK-Go fan duct v2 + Volcano hotend + inductive 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]
2022-10-08 expand bottom holes and use micky mouse ears by default
    [PTC heater box - with micky mouse ears.step, PTC heater box - with micky mouse ears.stl, PTC heater box.step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]
2022-10-09 Update a RRF all-in-one zip file for Octopus Pro F429
    [bed.g, config.g, heightmap.csv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]
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2022-10-09 add a note to lower duty cycle in some cases for the PTC heater
    [config.g]
2022-10-09 set the active temperature of tool 0 to zero, and select tool 0 immediately after boot
    [config.g]
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2022-10-11 update rear belt tensioner design for easier print. move it to the optional parts.
    [XY belt tensioner.stl, XY belt tensioners.step]
2022-10-11 move it to the optional parts and rename it "secondary" to align the manual
    [XY belt tensioner.stl, XY belt tensioners.step]
2022-10-11 add an X endstop clip for the Breezer remote duct
    [X endstop trigger cap - for Breezer remote cooling duct.step, X endstop trigger cap - for Breezer remote cooling duct.stl]
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2022-11-02 Upload a new bed expansion mount for the right leg.
    [bed expansion mount.step, bed expansion mount.stl]
2022-11-08 Expand output, strength the arms, use sqaure nuts.
    [Cura 5.1.1 project of a SK-Cube fan duct + Volcano hotend.3mf, Cura 5.1.1 project of a SK-Cube fan duct v2 + Volcano hotend + inductive ABL for SK-Cube.3mf, SK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]
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2022-11-13 slightly modify dimentions for easiler fitting. move this filament guide holder to the must directory.
    [filament PTFE guide holder.step, filament PTFE guide holder.stl]
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2022-11-24 Lower the default max XY moving speed to 350mm/s or 21000mm/min based on the max 1000 RPM of MKS Servo42C.
    [config.g, printer (chamber heater).cfg]
2022-12-01 Add an activated charcoal cartridge for the PTC heater box
    [Activated charcoal cartridge.step, Activated charcoal cartridge.stl, Cartidge cover.step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]
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2022-12-10 the cartridge is moved to the middle for more contact area to the activated charcoal, and becomes narrower for more air to blow to the heater.
    [Activated charcoal cartridge A.step, Activated charcoal cartridge A.stl, Activated charcoal cartridge B.step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]
2022-12-11 add mouse ears for better 1st layer adhesion
    [activated charcoal cartridge.step, activated charcoal cartridge.stl]
2022-12-11 refine design: thicken and stiffen covers
    [activated charcoal cartridge.step, activated charcoal cartridge.stl, cover A.step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]
2022-12-11 update 2 versions of screen sizes, 3.0mm & 0.8mm
    [0_8mm activated charcoal cartridge.step, 0_8mm activated charcoal cartridge.stl, 0_8mm cover A.step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]
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2024-10-20 add a new version of PTC heater box which is less possible to warp and no support needed.
    [box_half_a.stl, box_half_b.stl, panel_bottom.stl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]
